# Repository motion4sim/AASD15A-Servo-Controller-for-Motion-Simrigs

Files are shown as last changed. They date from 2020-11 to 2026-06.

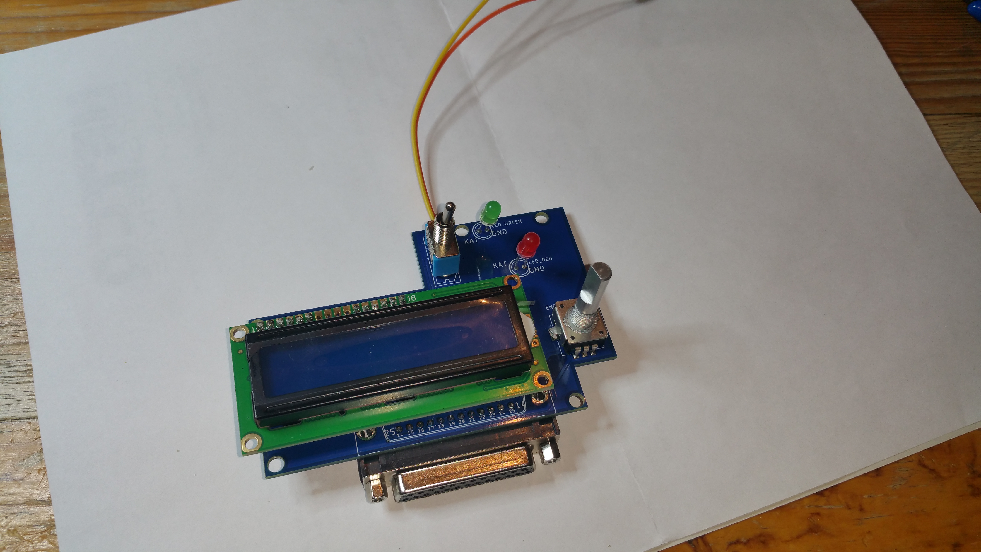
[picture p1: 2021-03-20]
diy_handheld/handheld-pcb-version/handheld-pcb-1 (3).jpg

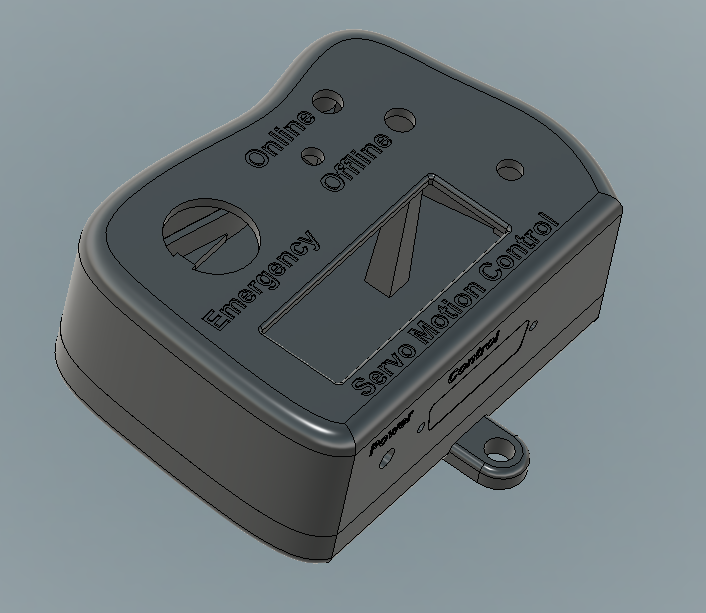
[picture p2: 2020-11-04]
diy_handheld/handheld_1.png

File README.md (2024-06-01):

# AASD15A-Servo-Controller-for-Motion-Simrigs

checkout our shop at motion4sim.com for more information

Motion4Sim M4S Controller Firmware

Version v3.30

- factory reset required after flashing!!!
- added Actuator Input Data matrix, 
- so you can use SRS or Simtools Actuator order without reconnecting cables
- edit via Handheld in Actuators menu or use Dashboard in Filter tab
- only for direct mode!
- in position mode you will need still clockwise actuator connection starting with 1 at front left actuator 
- fixed shutdown function torque recognition and not rebooting
- fixed service menu torque recognition

Version 3.29

- added separate fifo for usb motion and data
- in principle, both USB ports can be operated in parallel
  need to test what happens when Motion data is received on both ports
  so be carefull using it
- changed debouncing for killswitch and online switch
- improvement of serial pattern detection
- added SimHub  support

Version 3.28 

- added message crc datachecks to all communication 
- the end chars 0x0a 0x0d are replaced with crc16 checksumm
- still back compatible to 0x0a 0x0d if send to recieve but sends only with crc so older dashboard will not recieve data
- update to Dashboard Version 3.28
- works only full with Dashboard >=v3.28 because crc checks
- fixed motionusb port problems

Version 3.26

- just for testing fw updates with flypt

Version 3.25 fix1

- fixed  short brake release impulse when startup with EM Button engaged
- fixed  online speed set to 50khz only in some conditions

Version 3.25 official

- hardware pulsing is stable now ,just enable, works same, read advice in dashboard
- small change to break release delaytiming
- new spike algorithm is now implemented 
	-> adjust spikwindow for setup from smaller value to higher
	-> read also fw3.15 release note down this list
- old spike is emalp+spike2 option now in filter setting
- changed lowspeed in factory settings
- changed breakdelay to 100ms in factory settings
- @dureiken changed factory setting motionxp for spike to spike2 and cal/lowspeed settings
- no changes to dashboard made same version 

Version 3.24 

- a lot of changes test your rig behaviour before pratical use!!
- added new EM Button debouncing with Software and Hardware
- added prompt ">" for Setup and Configuration values
- fixed flashport at startup wrong config  data transmission 
- added transition to standby with special triple emalp filtering, 
	-> also into motion from standby uses now this transition
	-> setup transition speed for this its in seconds
- maybe for better transition adjust the low speed to 5000*10hz in setup (Speed from/to Standby Position)
	-> this also changes auto homeing speed for belt
- hardcoded service speed set to 1000x10hz before was low speed too
- extra01 pin is now low at startup in case for brake nc use
- controller firmware reset, now only possible in save rig states
- dashboard controls "transmit"  accepted only when restart/offline phase possible
- fixing service menu emergency issues
- changed doubleclick recognition speed a little bit faster 
- fixed belt spike2 problem (no spike calculation for belt)
- removed doubleclick feature in the menu

Version 3.20

-  removed motionsystem introduced in 3.10 -> done by Dashboard now
-  added support for flash-usb port for motion and dashboard use
-> i recommend this port now for all operations
-  added hw pulsing support for pcb version from 1.09 (could double resolution)
-  added option for inoffz. srs supp with native usbport mod
-  added support for new motioncueingsystem included in dashboard now
-  this fw operates only with dashboard version 3.20 
-  added realtime belt retreat modification 
-  added adjust.servobrake switching delay

Version 3.15 

- lcd init problems fixed everything else seems to emi related
- lcd only comes to garbled char when workhour timer is active (normaly deactivated)
- option in menu -> setup -> Mastergain enabl : if set to off Mastergain is fixed on main screen
- long press (>3s) of encoder button does a lcd screen init
- double click feature for encoder button
	-> fast double click switches main screen from 
		gain"100%" -> "Sp Win" Spike Window -> "Belt" retreat -> "Filter" Emalp value back to gain
	-> you can change value with encoder turning left or right
	-> values were not saved to eeprom
	-> for saving go to menu "Save and return"
	-> with double click you can also leave any menu back to main screen with no saving
- new Spike Filter design
	
	defined with 3 Values.
	
		Menu -> Filter 	-> Spike Filter 	
				-> Spike Window
				-> Sp.Filter smooth

	-> Spike Window:  from 1...400% (or more) 100%  is 1/4 actuator range in pulses
    	 	-this means if pulse input is more than say 100% (1/4 of actuator stroke) Spike is detected
		-pulsestrain is cut/limited to Spike window size pulsecount
	-> Spike Filter: 
 		- after Spike detection the Emalp(normal Filter) raises every frame(2ms) Spikestrength value is lowpass over raising emalp	
		-> this means lower value faster growing Filter (after spike slower return to normal motion)
		-> higher value ,lower growing filter ( after spike faster return to normal motion)
	-> Sp. Filter smooth:  when spike is finished (pulsetrain smaller as Spike Window)
		-> dyn Emalp filter decreases(2ms) with  Sp.Filter smooth ( Emalp over decr. value) 
		-> this means higher value slower decrease and slower return to normal motion
		-> and vice versa
	
	//for me follwing values have worked
	//Spikestrength = 20 to 80  (higher means more smooth in spike)
	//Spikewindow from 10%  for racing 20-40 % for flying  (higher means later spike detection)
	//Spike smooth 2-10   (higher means longer of spike smoothing ,do not use 1 never ending spike) 

Version 3.11 release

continueing lcd fixes
watch also 3.10 notice
- long press (5s) of encoder button does a lcd screen init

Version 3.10 release

Pay attention Motioncueingsystem is W.I.P. start with low scale first
Factory Reset is important for Motioncueingsystem to work
please install also latest Dashboard v3.10 for full use of Motioncueingsystem

-added full scripting motioncueing and filtersystem
-added autotuning system to scale the motioncueing profiles
-added system for storing motionprofiles in flash
-added doubleclick feautre for inputsystem
-added function to boot intobootloader in setup menu
-added support for new pcbversion 1.09 hardwaretimers

Version 2.23 release

- added dashboard support for belt configuration
- added working hour meter reset support ( press user button > 15 seconds for reset)
- lcd working now with no problems
- this fw support only until pcb v. 1.08
- last fw for this boards
- some code improvements

Version 2.19 release

- added belt actuator support
- added new emergency mode "keep online"
- added extra01 function send timer signal
- added sineloop for testing actuators
- added working hour meter
- factory reset needed from fw 2.11
- fixed most lcd problems but still not all yet :(
- better code perfomance
- cleanup 

Version 2.11

- added  support for SFX 3 actor  System in position mode
- no factory reset needed
- fixed homing issue with linear systems other then 6dof
- lcd garbage issue still exist _ screen reinit time now is shorter

Version 2.01

-complete rewrite of the motion engine
-now best motion ever 
-some smaler bugfixes (Service Menu)
-led blinking in some states
-code cleanup
-rewrite of serial port code
-rewrite of lcd display routines
-no srs support :)
Attention - for older first series boards there is also necessary to update the bootloader, contact me for this !!!

Version 1.60 Factory reset needed !! storage  changed

- included SFX RIG types in kinematics calculation BETA!
- activatet Native USB Port to work with Dashboard APP and Motiondata ->still not good as it should use MotionData port
- improved interface to Dashboard App
- load and Install also new Dashboard App

Version 1.54

- serial data interface  transfer extended for new Dashboard App
- works only with new DasBoard App correct,please update
- always do a factory reset after flash
- some bugfixes, linear factory reset, and 6dof float mode
- fixed srs

Version 1.51

Attention:	Factory reset needed !! storage  changed

- rewrite of service actuator moving functions
- usersettings moved to internal MCU flash storage  -> factory reset needed ! 
- factory reset possible with on board button (press 4 seconds for rotating Act setting and 8 seconds for linear Act settings)  
- stability of usb for apps improved
- update also to latest apps

Version 1.47

Attention: 	- eeprom data changed  _ after flashing do factory reset !

- fixed some servo7 bugs
- fixed linear actuator safety bug (safety >pitch)
- added function for servobrakes WIP
- added new transition to motion
- added adjustable time for transition to motion
- added offset for linear actuators
- added adjustable Online Position
- added adjustable Maximum Gain
- better actuator check function (also while homing)
- added shutdown function (drives actuators down to homing point and powers servos off; turn left in menu ) 
- smaller changes in menu texts
- some value checks added
- most new settings only from handheld adjustable actually

thanks to Dirty for testing

Version 1.42

Attention: 	- eeprom data changed  _ after flashing do factory reset !
		- save your settings to paper!! remote App changed data completely
		- install new Handheld app version
		- install new config app version

- added fully support for servo 7 ( remove some resistors on board before use)
- added support for infinite actuators
- bug fix of version 1.41_fix1 display stuck after flash
- some bugs fixed in srs autoconnect
- smaller changes in menu texts
- fixed bugs with remote handheld app
- changed actuator check function 

Version 1.41

-added interface for remote handheld app at native usb port
  (u have to wire the native usb port)
- minor code changes
- spikefilter led keeps on bug fixed
- transmit data from app doesnt reboot  fixed
- memory protection feauture inkluded
- updated bootloader for automatic software bootloadermode ( board delivered later as 062821)

Version 1.30

- added few remote commands for remote app testing features
- now fw has support for Sim Racing Studio in amcsd15a mode
- changed filter timing 
- minor bugfixes and code changes

Version 1.20

Attention: 	- eeprom data changed  _ after flashing do factory reset !
		- save your settings to paper remote App changed data completely

- complete new actuator settings, each actuator can be different , special for linear rigs seatmover
- keys and buttons using interrupts now
- native usb port on same70 board only for fw update
- remote app works now only with motion data port on breakout port
- remote app new version release for this firmware
- lcd fps setting now working
- new option for encoder direction

Version 1.19

- new data mode for floating point values from flypt mover
- changed some  motion cueing calculation for linear actuators
- improved 3d calculation to support center of rotation 
- fixed emergency button problems
- factory reset available for linear and rotating actuators
- remote app some minor changes
- fixed bug loading factory data when using remote app before calibrating

Version 1.18

- remote app expanded ,for now function only to native usb port
- native usb port and ftdi usb port working together now
- native usb port not for motiondata due to usb stack problems with pulse engine
- some changes to onboard motion cueing  now xyz koordsystem works like flypt
- motion cueing with linear 6dof rig works thanks to [GER]Basti-Discord

Version 1.17 Beta

- new usb remote configuration interface
- simple gui app  on github
- please check plattform after transmit configuration data controller will reset

Version  1.16 Beta

- change LCD - Display Init
- usb cdc code for target usb port (near ethernet connector) support asyn. cdc transfer
- enter bootloader via emergency-bt online-sw encoder-bt pressed and power on
- modified calculation of rotat. and linear inverse kinematics

W.I.P.

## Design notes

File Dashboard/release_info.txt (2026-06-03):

Motion4Sim DashBoard App

Disclaimer! this Software is free to use and in development. 
we explain that the controller from Motion4Sim is working indepently
and there is no need to use this software to operate.
we assume no liability for any damage caused by use.  
you use it at your own risk.

Release v5.36.2

- Hotfix for fw 5.37 Spike filter switching 
  -> related to fw changes
- added extension json config files for EC config data  

Release v5.36

- added new Onlinebutton Settings Latching NO/NC Momentary NC/NO
- correction of some Rig presets
- added WebDashboard URL configuration

Release v5.35

- added new Rigtypes support
- added shutdown backoff for actuator shutdown function
- update fw update with fw check and downloader
- added auto token function for offline license activation 

Release v5.34

- updated cfg exchange system to CBOR for increased flexibility
- switched cfg files to JSON (compatible with web dashboard cfg files)
note: older cfg files are still supported — load them and verify the configuration
- changed motor speed unit from frequency to RPM
- added EtherCAT configuration tab
- various minor improvements and fixes
- works with STm fw and latest Atmel fw

Release v4.30

- added support for Actuator8 WIND
- added presetmanager, when add new profile to motionsystem
- added wind support for motionsystem ( nolimits & xplane source support now wind) more to come
- added new Filter Syntaxes :
	ADD(VALUE; number)
	SETVALUE(VALUE; number)

Release v4.29

- new Inno Setup Installer ,small version github
  if it fails install manually before 
	-dotNetFx472_Full_x86_x64.exe
        -vc_redist.x64.exe 

- fixed cw/ccw showed wrong in actuator settings
- added lic update support for pro controllers

- new motion system with a lot of new features
- graphic Motion Telemetry Output
- 3d View for 6dof Rigs
- added new Belt Force System w.i.p.
- added Wind output to Com (experimental not directly tested)
- added OXRMC config GUI,when installed
- added basic mover import (limited function, only for filterstrings and 1. Pose is primary and second is ground)
- added Extra Effects Generator (Noise and Sinus only atm) 
  -> Noise can be casaded to have Asphalt layer maybe w.i.p.

- old profiles still supported import them

- added new gamesource Eurp.Trucksimulator2 &American Truck Sim.
- added Assetto Corsa Evo supp.
- fixed Nolimits2 gimbal lock problem
 
  Attention!!

  1. backup your profile from %appdata%/Roaming/Motion4Sim/motionprofile.xml
     normally it will not overwrite, but to be sure you have it save
  2. please be carefull its w.i.p. maybe there are some things will not work or cause problems
     i spent lot of time with it but i know i couldnt test everything !!
  3. do not forget to enable motionsystem in Config ->Setup Tab for using
  4. for networks setups please disable motion when using other motioncueing
      otherwise it will send also data to the rig !!!!

Release v4.25 fix1  

- re upload not zipped for Win11 virus false detection problem

Release v4.25

- added Setup Options for Switch/PushButton
- fixed some Profile saving/loading Issues
- added Support for Torgue Mode Actuator 7

Release v4.24

- added check for fw bin files, checks files for integrity (works from fw 4.24 no support for older fw files)
- added crc for bin
- checked source Condor2 is working also for Condor3
- added eth lan adapter checks

Release v4.22

- added latest values to edit from Dashboard
- added  udp support for new boards

Release v3.31

- added support for rFactor2 and F1-2024
- rFactor needs special plugin to work so 
- go to Config -> Source and  patch button will copy dll to rfactor plugin dir
- fixed config window minimize bug

Release v3.30

- config works only with fw 3.30 
- added Actuator Input Data matrix, 
- so you can use SRS or Simtools Actuator order without reconnecting
- edit via Handheld in Actuators menu or use Dashboard in Filter tab
- only for direct mode 
- in position mode you will need clockwise actuator connection starting with 1 at front left actuator 

Release v3.29

- added Source LFS
- added patching for LFS
- fixed flickering source combobox when connected, now combo is disabled
- fixed wrong gamedetecting  F1_23;DCS;Dirt when using same udp port
- fixed  ACC
- improved some gamedetection

Release v3.28++testing

- added  Source
	Nolimits2
	Automobilista2
	iRacing
	WRC
	BeamNG
- added Mover import for Filterstrings only
- added Patching for sources to work
- added support for different  motionprofile presets and smart editor for it		

Release v3.28

-added F1-2023 Game Source
-added Condor2 Soaring Source
-fixed  crc Problems with older FW
-for existing Installation add Profile from /program/motion4sim/profiles/motionprofile.xml
-or replace in %appdata%/motion4sim .. you can backup this file and reload your old profiles
-installer will not overwrite 
-added smart controller support

Release v3.28 testing - not much tested so far but works here  therefore it is tesing release

- added Dirt Rally 2.0 Dirt 4 support
- added crc checksums for data transmission
- added fw update checking and downloading
- added patch support for DCS and Dirt Rally 
- added openxr mc support in motionsystem
- added belt support for actuator 7 in motionsystem
- added profile  import and export features
- testing2: fixed comport vector overflow with mostly motionusb
- testing2: fixed msfs source not disconnect when closing msfs
- testing3: fixed xmlfileimport mapping
- testing3: changed german error lang
- testing4: added oxrmc changing gain with controller gain

Release v3.24

- added check for Transmit to prevent from restarting the controller 
  in unsafe situations

Release v3.20

- added Filter based Motion Cueing System 
- added Xplane, MSFS2020, DCS, Assetto Corsa Comp., Raceroom Source
- added High/Low Precise Timers for Filtersystem
- fixed Testpage bad Motion
- added support for Flash USB Port
- added some Option on Setup page
- only works with fw 3.20
- added some checks
- changed installer lang to english
- fixed em-state und extra01 state to combo boxes

Release v3.10

- added support for Motioncueingsystem
- fw 3.10 is recommend

Release v2.18 

- added belt config
- added disable autoconnect
- added using standart "comport" feature
- complete new code for communication
- testet with win 10 only
- changed and cleanup layout
- needs fw >2.23

Release v2.16 still Beta

- fixed homing speed data
- fixed crashing  App sometimes special with ftdi boards
- some layout changes
- added sfx 3 actor systems
- fw  >2.15

Release v2.15 Beta

- fixed flashing not working
- fixed autoconnect

Release v2.10 Beta

- code speedup
- changed Joysticksupport
- removed some buggy feautres
- underlaying api complete rewrite
- improved serial data connection

Release v1.60

thanks to Milligaus for developing C# Interface

- Handheld support to use controller with software only
- Configuration of all Settings in Config section of App
- Actuator 7 configuration will follow soon
- Memory Mapped File (MMF) support to run in Background while using Mover or Simtools
- UDP support is planned
- Software Keys and Buttons could assigned for OnlineSwitch and Emergency Switch functions
- Support for Gamepads,Joystick Keyboard Buttons (W.I.P.)

- sometimes problems with bluethoot devices please deactivate to be proove

for Memory Mapped File use

"Motion4Sim_tx"  to send data to Controller from Mover etc
or
"Motion4Sim_rx" to recieve answers from Controller

please report bugs to discord (Motion4Sim@4206)

thanks for using

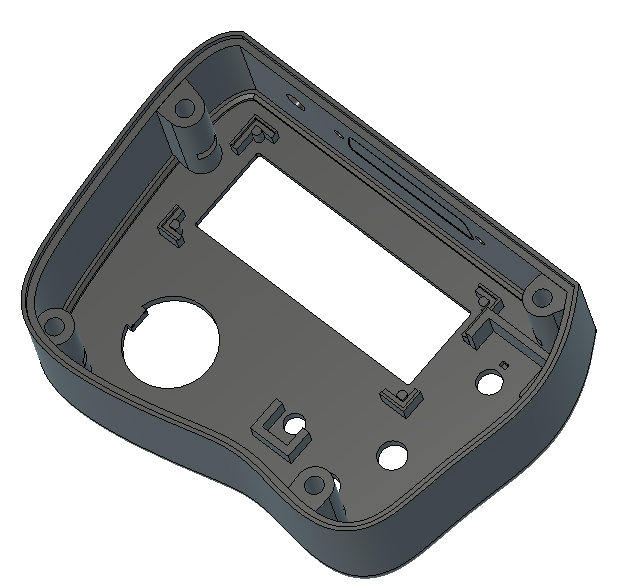
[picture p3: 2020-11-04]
diy_handheld/handheld3.png

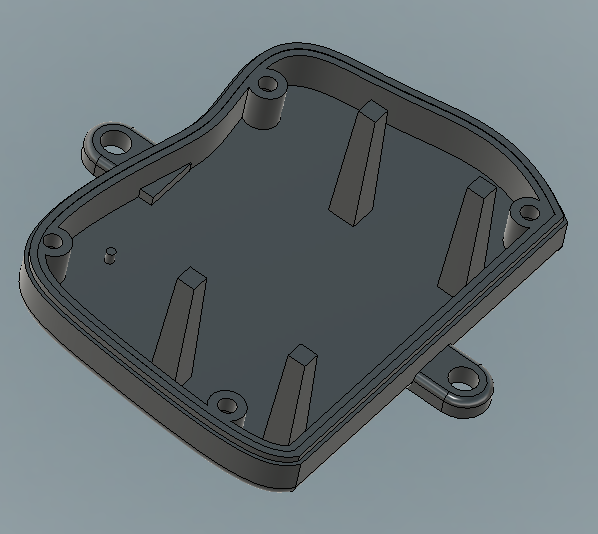
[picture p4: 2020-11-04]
diy_handheld/handheld2.png

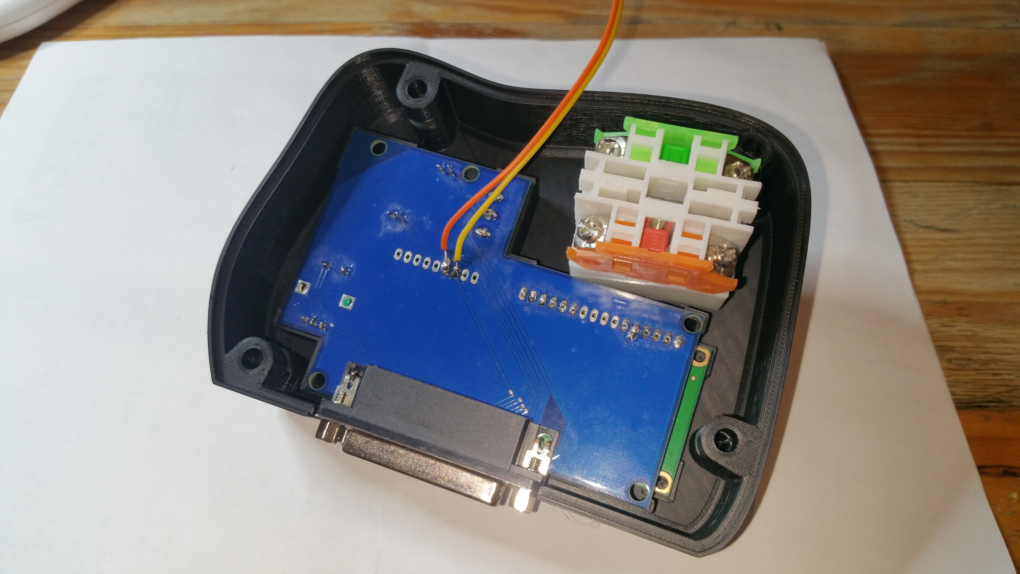
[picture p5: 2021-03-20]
diy_handheld/handheld-pcb-version/handheld-pcb-1 (4).jpg

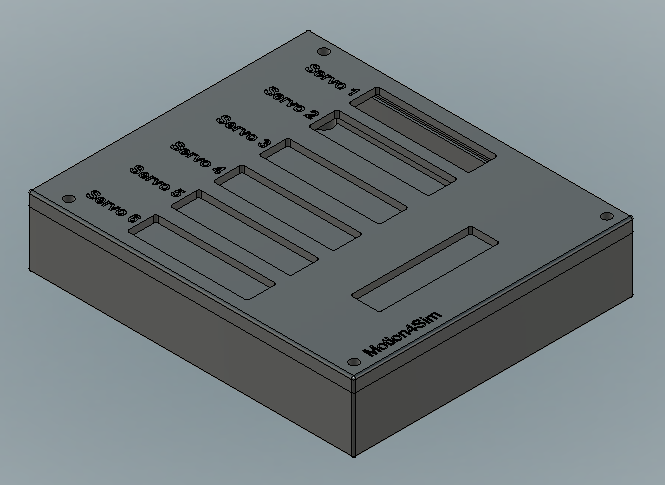
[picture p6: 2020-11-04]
diy_handheld/c_case_oben.png

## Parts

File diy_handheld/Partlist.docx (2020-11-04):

Partlist

1. Display 16x2

#### https://www.ebay.de/itm/LCD-1602-Blau-Display-HD44780-I2C-Anzeige-Bildschirm-16x2-Arduino-Raspberry-Pi/253723898777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

2. Encoder

###### https://www.ebay.de/itm/Rotary-Encoder-Drehregler-KY-040-Drehgeber-Taster-Poti-Arduino-Raspberry-Pi/392878965464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

3. Emergency Switch LAY37

###### https://www.ebay.de/itm/Not-Aus-Not-Aus-Schalter-Emergency-Stop-Pilzkopfschalter-Mushroom-head/162561518442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

4. Online Switch

###### https://www.ebay.de/itm/2x-MINI-KIPPSCHALTER-WIPPSCHALTER-KILLSWITCH-ECKIG-6MM-3A-KFZ-12V-VOLT/263098565064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

5. DB 25 Connector for solder female

https://www.ebay.de/itm/D-SUB-Buchse-25-polig-Lotkelch/184254619899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

1. 5V LED green and red

https://www.ebay.de/itm/3mm-LED-Sortiment-3-3V-5V-6V-9V-12V-red-blue-white-yellow-green-purple-12-Teile/283302538340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

1. holder for 5V Led

https://www.ebay.de/itm/10-Ledfassungen-f%C3%BCr-5mm-Leds-in-METALLOPTIK-Led-Fassung-Halterung-Montagefassung/370395657130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

4x Screw M4 x 30 mm and Nuts

some cable and solder tools

some pin male and female , shrink tubing

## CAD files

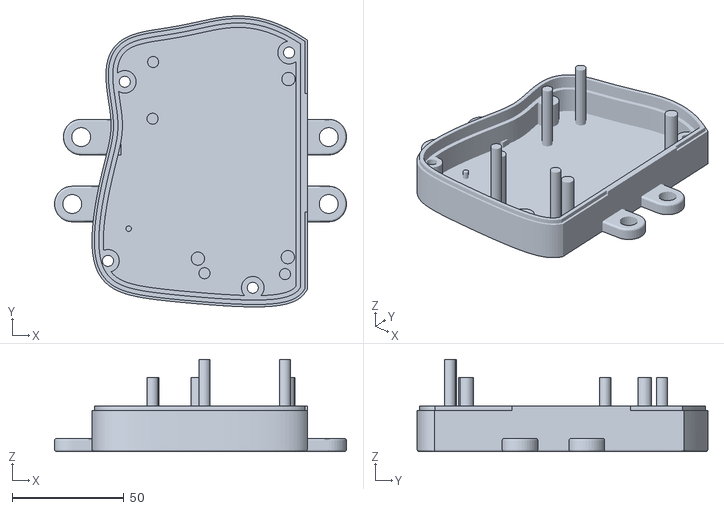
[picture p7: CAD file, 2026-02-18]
3d_print_files/handheld_back_pcb_30.stl
130.9 x 130.4 x 41.4

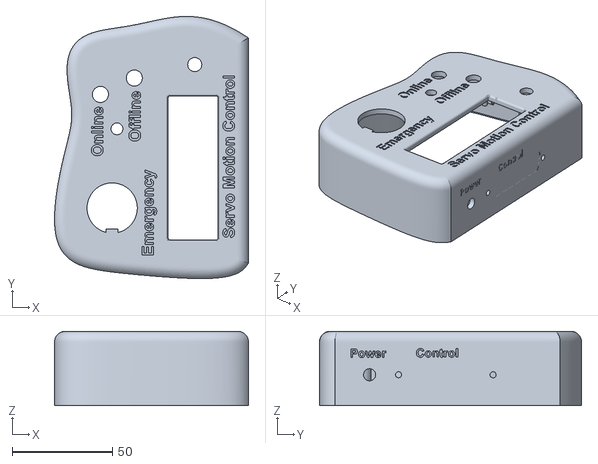
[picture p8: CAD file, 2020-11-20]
diy_handheld/Handheld_diy_top.stl
96.5 x 130.4 x 37.0

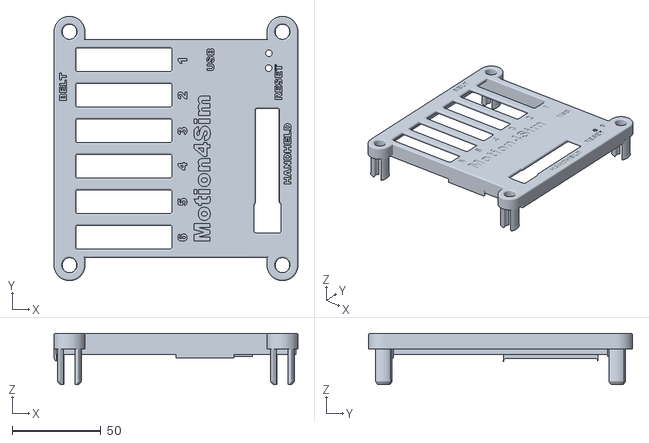
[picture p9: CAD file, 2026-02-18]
3d_print_files/pcb_top_m4s_v303.stl
137.5 x 148.9 x 29.0

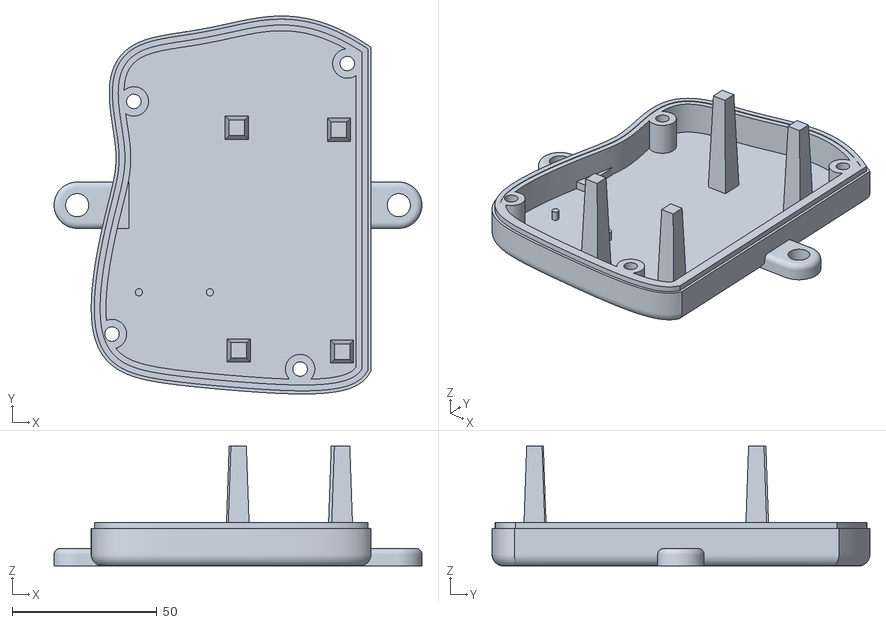
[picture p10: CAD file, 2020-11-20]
diy_handheld/Handheld_diy_back.stl
127.0 x 130.5 x 41.4

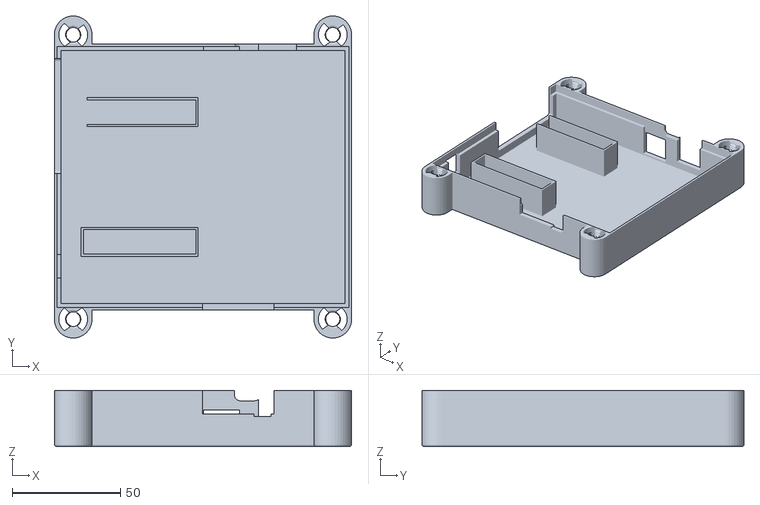
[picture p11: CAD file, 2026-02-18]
3d_print_files/pcb_btm_m4s_v303.stl
137.5 x 148.9 x 26.0

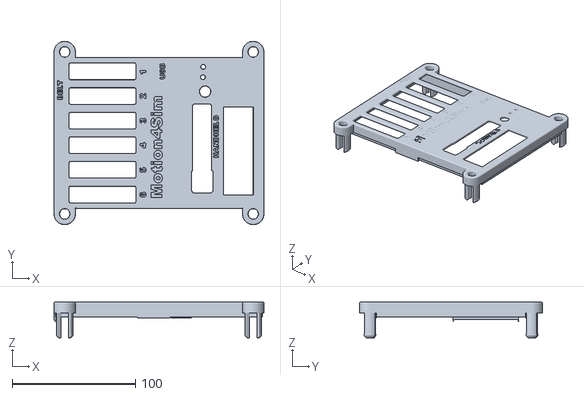
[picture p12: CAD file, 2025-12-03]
3d_print_files/pcb_case_display_top_motion4sim_v203.stl
170.5 x 148.9 x 29.0

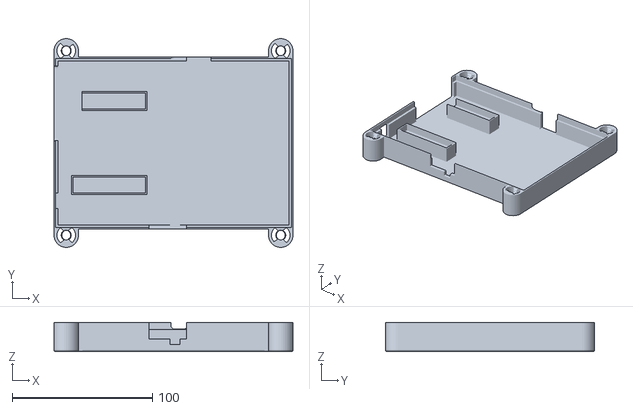
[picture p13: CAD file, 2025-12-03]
3d_print_files/pcb_case_display_bottom_motion4sim_v203.stl
170.5 x 148.9 x 21.0

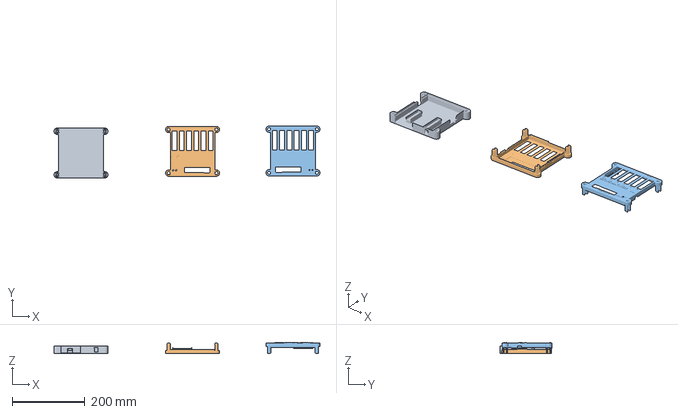
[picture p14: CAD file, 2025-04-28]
3d_print_files/2ColorPCBCase.3mf
732.6 x 143.0 x 31.4 mm
pcb-case_m4s_v203_bottom.stl
exported flat.stl x 2

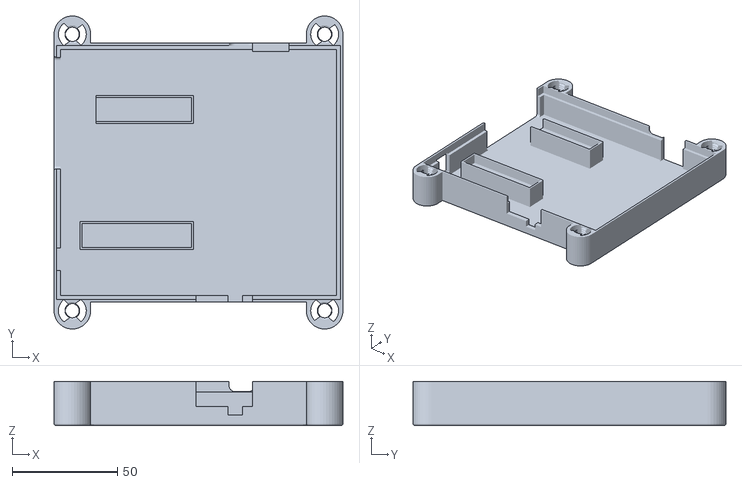
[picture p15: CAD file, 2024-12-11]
3d_print_files/pcb-case_m4s_v203_bottom.stl
137.5 x 148.9 x 21.0

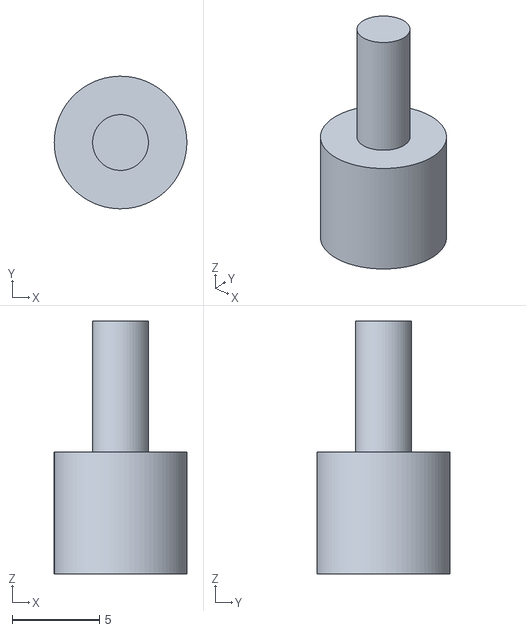
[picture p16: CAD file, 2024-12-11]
3d_print_files/pcb_case_button_v203.stl
7.60 x 7.60 x 14.5

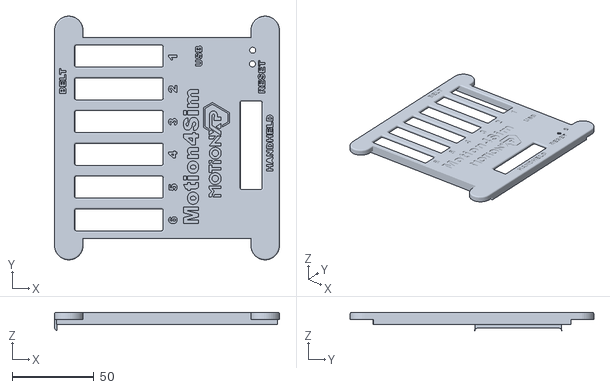
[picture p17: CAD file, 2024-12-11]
3d_print_files/pcb_case_top_motionxp_v203.stl
137.5 x 148.9 x 11.2

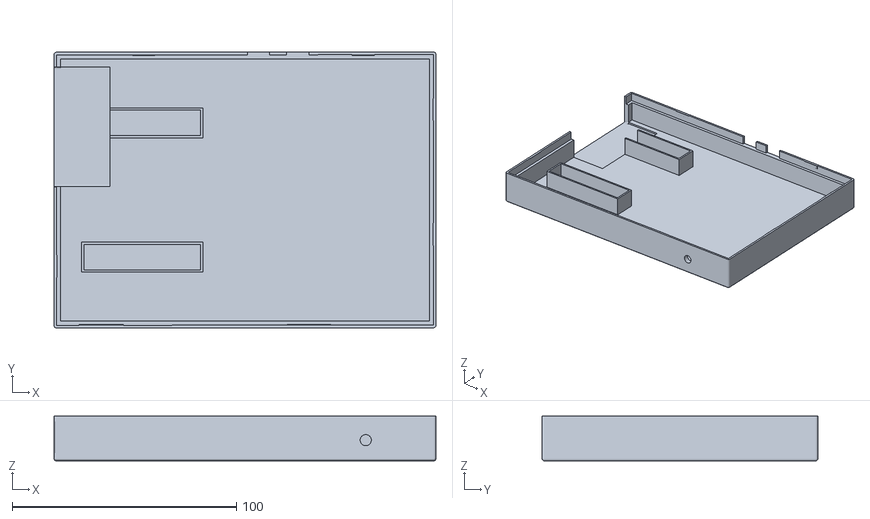
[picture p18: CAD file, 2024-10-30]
3d_print_files/gehäuse_bottom_pcb_v115mitdisplay.stl
170.5 x 123.0 x 20.0

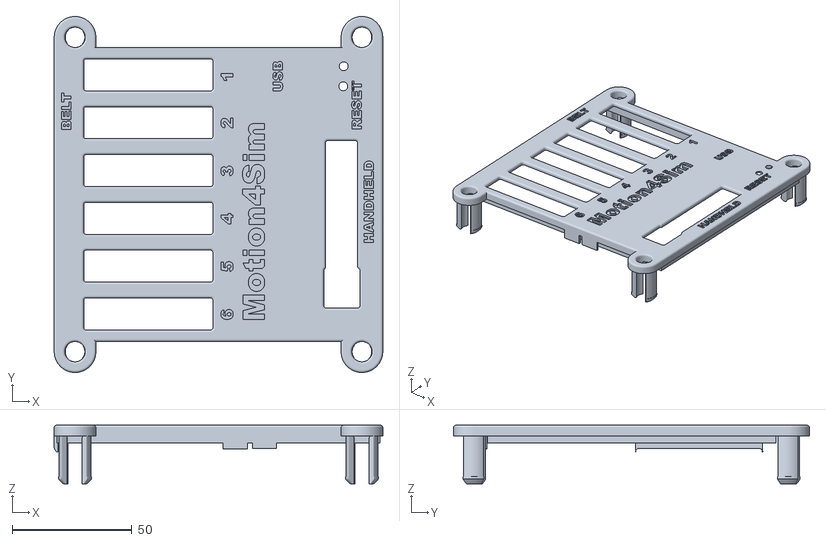
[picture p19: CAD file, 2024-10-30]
3d_print_files/Case_Top_m4s_1.15.stl
137.5 x 148.9 x 24.5

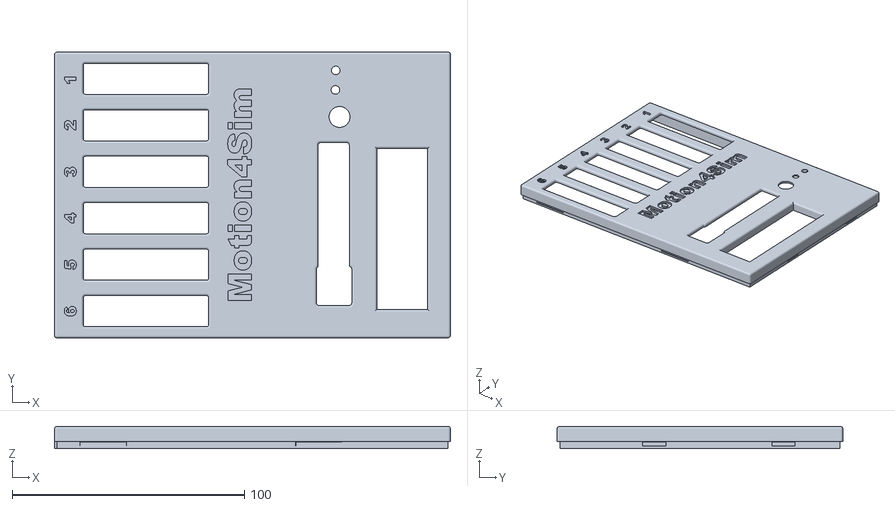
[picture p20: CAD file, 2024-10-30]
3d_print_files/gehäuse_top_pcb_v115mitdisplay.stl
170.5 x 123.0 x 9.50

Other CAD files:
3d_print_files/pcb_case_top_motion4sim_v203.stl
3d_print_files/gehäuse_top_pcb_v110_display.stl
3d_print_files/pcbcase_v1.10_button.stl
3d_print_files/gehäuse_down_pcb_v110_display.stl
3d_print_files/handheld_top_pcb.stl
3d_print_files/old_board/Controller_case_oben_lcd_enc_v1_04.stl
3d_print_files/old_board/Controller_case_oben_v1_04.stl
3d_print_files/old_board/Controller_case_unten_lcd_enc_v1_04.stl
3d_print_files/old_board/Controller_case_unten_v1_04.stl
3d_print_files/old_board/gehäuse_down_pcb_v110_display.stl
3d_print_files/old_board/gehäuse_top_pcb_v110_display.stl
3d_print_files/old_board/pcb_case_1.07_mysimkit_bottom.stl
3d_print_files/old_board/pcb_case_motion4sim_down_v1.10.stl
3d_print_files/old_board/pcb_case_motionxp_top_v1.09.stl
3d_print_files/old_board/pcb_case_motionxp_top_v1.10.stl
3d_print_files/old_board/pcb_case_mysimkit_down_v1.09.stl
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

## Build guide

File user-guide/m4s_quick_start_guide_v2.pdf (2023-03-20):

# Motion4Sim

2023

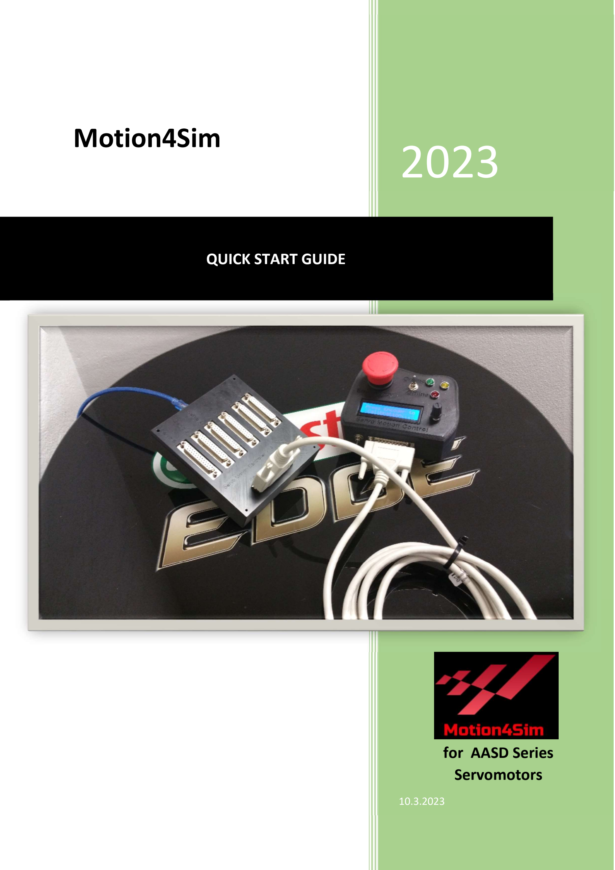
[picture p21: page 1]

for AASD Series
Servomotors

10.3.2023

QUICK START GUIDE

f o r b e t t e r

pe r f o r m a n c e

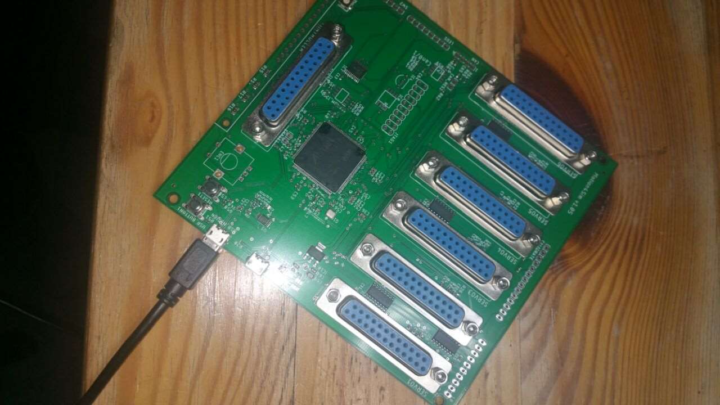
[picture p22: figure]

1

In these instructions we briefly describe how you can quickly put the controller into operation. For the first test, please use the motors without a connected load. Please be aware of the risk of injury if you use the motors improperly. For Information not described here, please read the manual.

### 1. make sure that the servo motors are not supplied with power

### 2. connect all cables needed to the motion4sim board

a. USB Cable to USB Motion Port on pcb board
b. D Sub 25 Cable 1-6 to the Servomotors (or opt. 7)
c. D Sub 25 Cable for handheld device if no display and encoder is installed
d. If display and encoder are installed , connect a online switch to connector SW2 and a emergency switch too (more details in the manual)
e. Or use the Dashboard app instead of c. or d.

### 3. Plugin the usb cable into computer or other 5v usb source

f o r b e t t e r

pe r f o r m a n c e

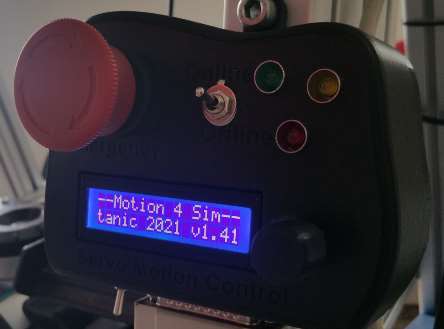
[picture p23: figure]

2

### 4. Controller boots up

### 5. Do factory reset by turning the encoder to the left and choose kind of

rotating- or linear actuator factory reset. enable with pressing encoder button. If the encoder works wrong direction check next point.

6. after the factory reset is done the controller resets and boots up again.

### 7. wait until is rebootet and press the encoder button

### 8. Check encoder turning direction , you can see the master gain rising or

reducing. Also check the behave oft the emergency button.

mastergain in the down left corner in %

right turn should rise and left turn should reduce master gain. It is possible that some encoders have other direction. This could be changed in the setup menu. (compare to manual)

f o r b e t t e r

pe r f o r m a n c e

3

### 9. Press encoder button and search by turning left/right the setup menu

entry. Press encoder button and turn encoder left/right until found „encoder direction“. If the emergency button is also not correct please change in the setup menu the option „Emergency NC“. Some emergency buttons are only „normaly open“ or „normaly closed“ other have both , in the setup menu you can change the behaviour oft he emergency button. If all settings are made, use the menuentry „back“ to get to the upper menu-level.

10. Now set the number of installed actuators in the menu. ->Actuators->Number Actuators(last entry)

The assignment of the connections is only important if you want to use the check actuator function. Otherwise the connections can be connected as you like. If you want use the check actuators function. Make sure to connect the actuators in such a way that the connections of the actuators in ascending order from 1 are fully occupied without any gaps. For example 1,2,3,4 or 1,2 or 1,2,3,4,5 and so on.

Now set all the actuator specific values.

Rig -> to Rotary or Linear Custom etc
Encoder PPR,
Electron.Gear ,

for rotating actuators:
Gearbox Ratio 1:,
Rot.Range,

for linear actuators:
Leadsrew Pitch,
Actuator Length
Lin. Act. Safety

Check also in
menu->Actuator->Actuators->Actuator1..8 submenu->Rotation:

f o r b e t t e r

pe r f o r m a n c e

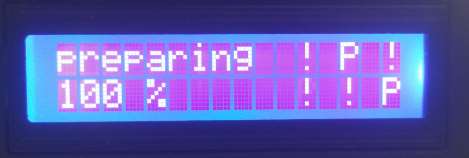
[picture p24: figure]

4

for cw or ccw rotation direction for each connected actuator.

most values are preset usefull

11.If all settings are done turn encoder to the rigth until you have a menu entry called „back“ , activate by pressing the encoder button. Repeat this until you have the upper menu and the last entry by turning to the rigth is „save and return“. Press encoder button to save the settings to eeprom. You have to use this function everytime you change values.

### 12. Only in the first run you should repower the controller , when all

settings have saved then execute the reset option in menu.

13.Now power the actuators.

14.After controller reboots press encoder to home.

15.The actuators should now searching for home position. They are searching for a hard stop or running for home switch to trigger. Check that all actuators are turning to the correct direction. If something goes wrong hit the emergency button for stop. Change the settings and repeat. Homing is essential for the controller to work properly.

The display shows :

X: for unconnected motors
P: for homing motors (preparing)
!: for running to park or safety position R: for Ready

f o r b e t t e r

pe r f o r m a n c e

5

16.If they are ready , the display shows „R“ for each actuator. You can switch off the online switch. If the switch is already at off position you can switch online and the actuator moves to standby position and is ready for recieving data.

### 17. Check the range oft the actuator carefully so that the selected values

causes no hard crash of your hardware

18.read the manual carefully, if you have problems contact support.

### 19. For easier configuration there is an Dashboard app. You can download

from here

https://github.com/motion4sim/AASD15A-Servo-Controller-for-Motion-Simrigs/tree/master/Dashboard
Please note the dashboard app has problems in win11 .
Close all Serial scanning apps like srs. If the app won´t connect to Controller please try following.
Remove all unneeded USB-Serial Devices and deactivate Bluetooth –Serial Devices.
If changes were made in the Configuration you always have to „Transmit“ the data to Controller.

### 20. thank you for using motion4sim and enjoy

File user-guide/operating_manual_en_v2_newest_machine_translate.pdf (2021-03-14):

# operation manual

2020

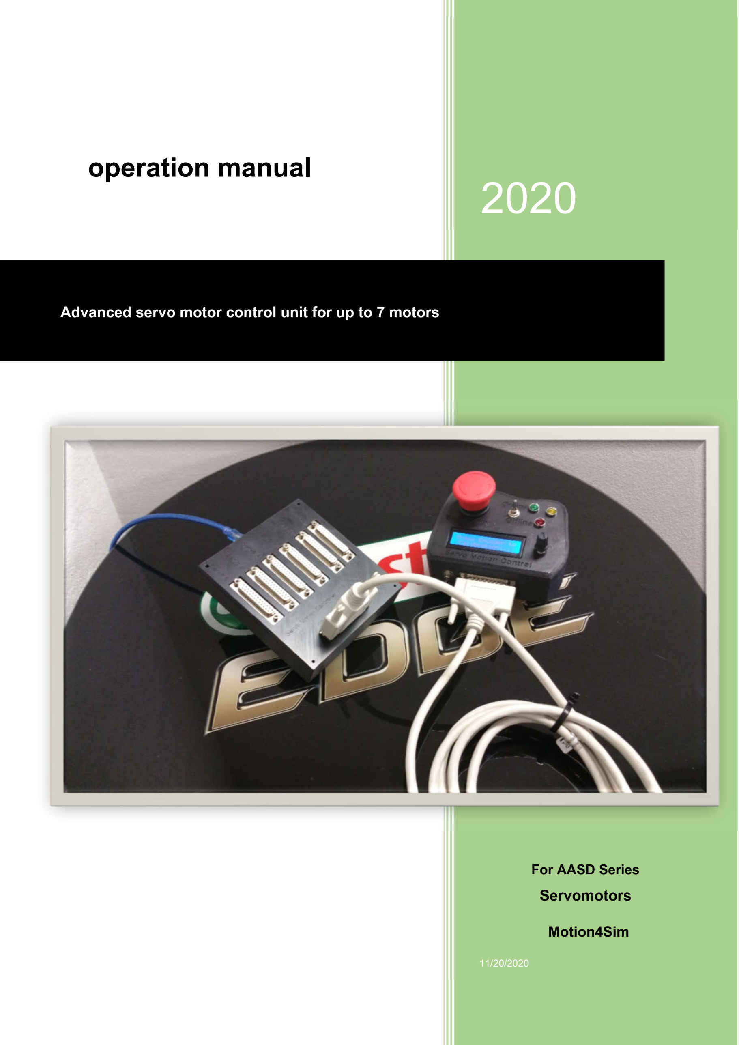
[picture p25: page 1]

## Advanced servo motor control unit for up to 7 motors

### For AASD Series

## Servomotors

### Motion4Sim

11/20/2020

## contents

Hardware cabling | 8th
Servo motor amplifier wiring | 8th
SET UP | 19th

1

introduction

The M4S-AASD15A servo controller enables the fast and seamless transfer of movement information from the PC simulation to the servo motor. The data exchange takes place between the interface programs such as Simtools, FLyPT Mover, BFF, etc. and the simulation.

The interface software calculates the motion vectors and forwards the values to the M4S servo controller via the USB interface. This controls the servomotors and also offers the option of calculating and smoothing motion cues yourself. The servo motor output stages are connected with DB25 cables.

All parameters necessary to operate the many actuators and actuator types are freely adjustable and configurable. All common servomotors that support STEP / DIR can be used.

2

## Functions

The controller was mainly designed for the AASD servos. However, other servomotors can also be operated with it. It can be used to operate all servomotors whose amplifiers are operated via the Step / Dir function.

The following functions are operated by the controller:

Hardware functions

1.
2.
3.

4th
5.

6th
7th
8th.
9.
10. 32 bit processor

### 11. Save the settings 12. Control of LEDs for status display (external handheld) 13. Housing (to print yourself)

14.Control unit can be installed 3m away (optional)

### 15. LC display and encoder can also be installed on the mainboard

### 16. Automatic home calibration on power up or re-connection without limit switches

### 17. Limit switches can be optionally installed for home calibration

### 18. Protection from exceeding physical limits of the actuator 19. Optional Platform Health check, to ensure all actuators are active during gaming 20. Latency as low as 1ms in Mover and Simtools or faster if some tool will support 21. E-stop, Force Offline buttons and switches

### 22. Usb power supply

Control of 6 + 1 servomotors (optional) Pulse speed up
to 550 kHz
Step / Dir fashion
Query and evaluation of torque (for calibration) as well as error status, display of parameters via LC display 16x2, full menu
Operation via rotary encoder with pushbutton switch for
signal reception
Emergency stop switch for the servo functions. Serial USB connection for data transfer

Software functions

1.
2.
3.

4th
5.

6th
7th
8th.
9.

### 10. Adjustable stroke unlimited

Software is menu-driven and easy to use
All functions can be parameterized to meet your own requirements. Monitoring of the status of the motors
Automatic calibration of the zero position Servomotors calibration also possible via limit switches
Service function for repair or control position of the motors Manual control of each motor individually for testing and maintenance Adjustable direction for Inline or Foldback placement of servomotor Adjustable screw lead pitch advance per revolution freely adjustable

3

### 11. Selection of belt reduction ratios or gear ratios freely adjustable

### 12. Rotating and linear actuators are supported

### 13. Scaling of the input signals (master gain)

### 14. Real exponential moving average filter for anti-vibration and smooth pulses on the

actuator
15. advanced full adjustable spike filter to automatically eliminate jolts during crashes or unwanted motion cues

### 16. Offset for each motor (especially for rotating actuators)

### 17. Variable parking position

18. Actuators individually adjustable (electronic translation, length of the act., DOF system)

### 19. Speeds for calibration, slow speed and high speed freely adjustable (max. 550 kHz)

20.Inverse kinematics with> 1000 calculations per second (for linear and non-linear actuators)

### 21. Geometry for steward platforms with 6 DOF and 6 actuators individually adjustable

### 22. Wash-out filter for each axis (can only be set with inverse kinematics)

### 23. Evaluation of 24 bit input data (Simtools / Mover)

### 24. Calculation in 32/64 bit for maximum smoothness of movement

25. 2 different operating modes: direct or inverse kinematics

4th

### PCB and connectors

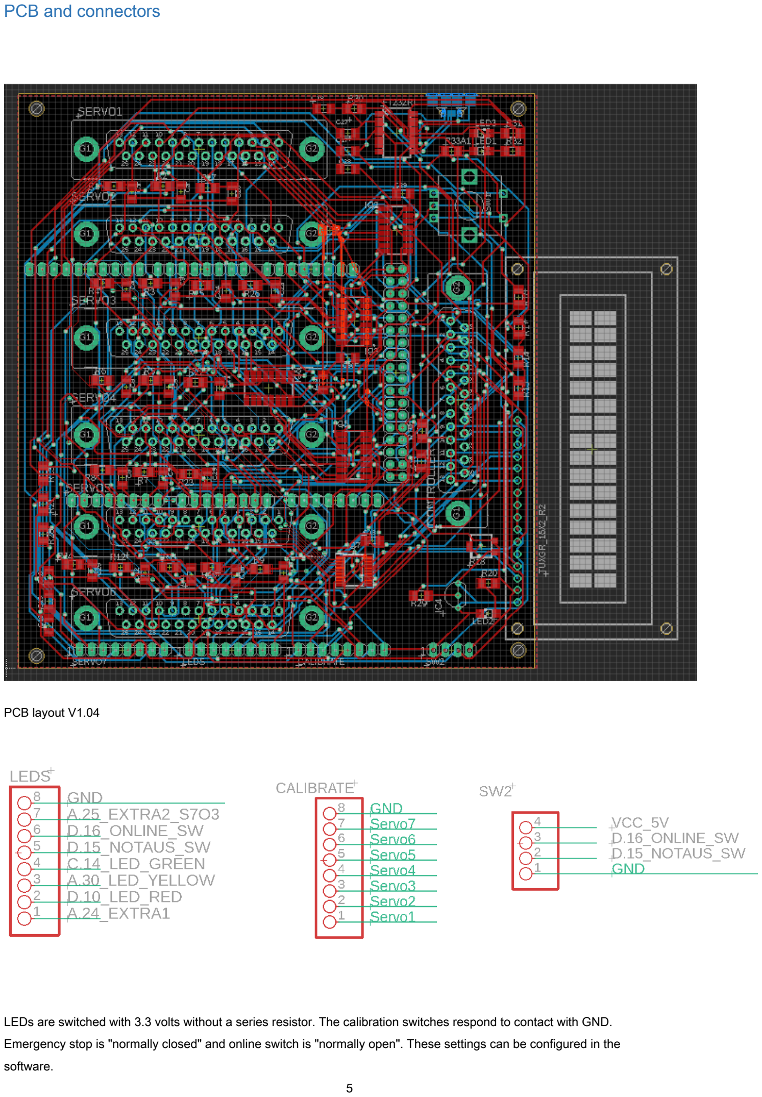
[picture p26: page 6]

PCB layout V1.04

LEDs are switched with 3.3 volts without a series resistor. The calibration switches respond to contact with GND. Emergency stop is "normally closed" and online switch is "normally open". These settings can be configured in the software.
5

Danger:

The micro USB port is sensitive to mechanical stress, please work with caution when trying it out.

Handheld Connector

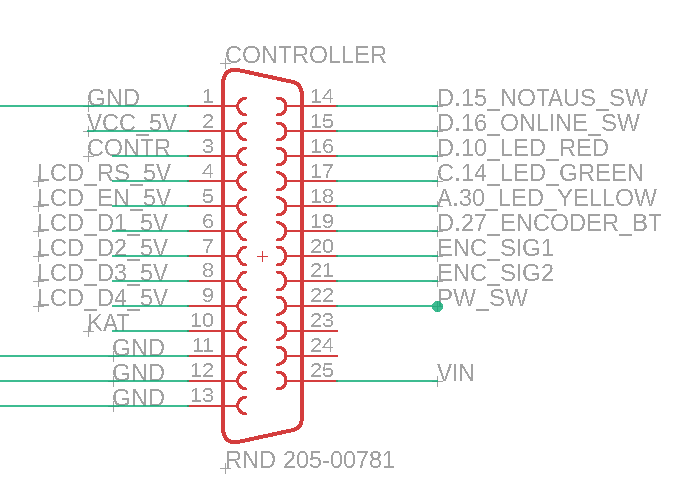
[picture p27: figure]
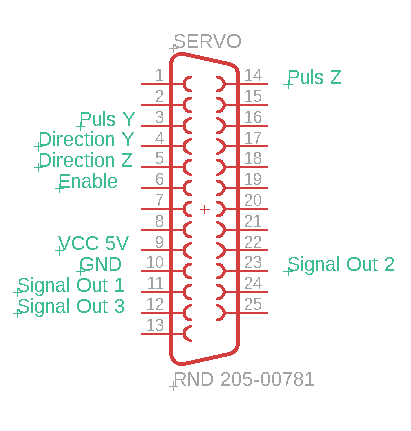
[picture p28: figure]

6th

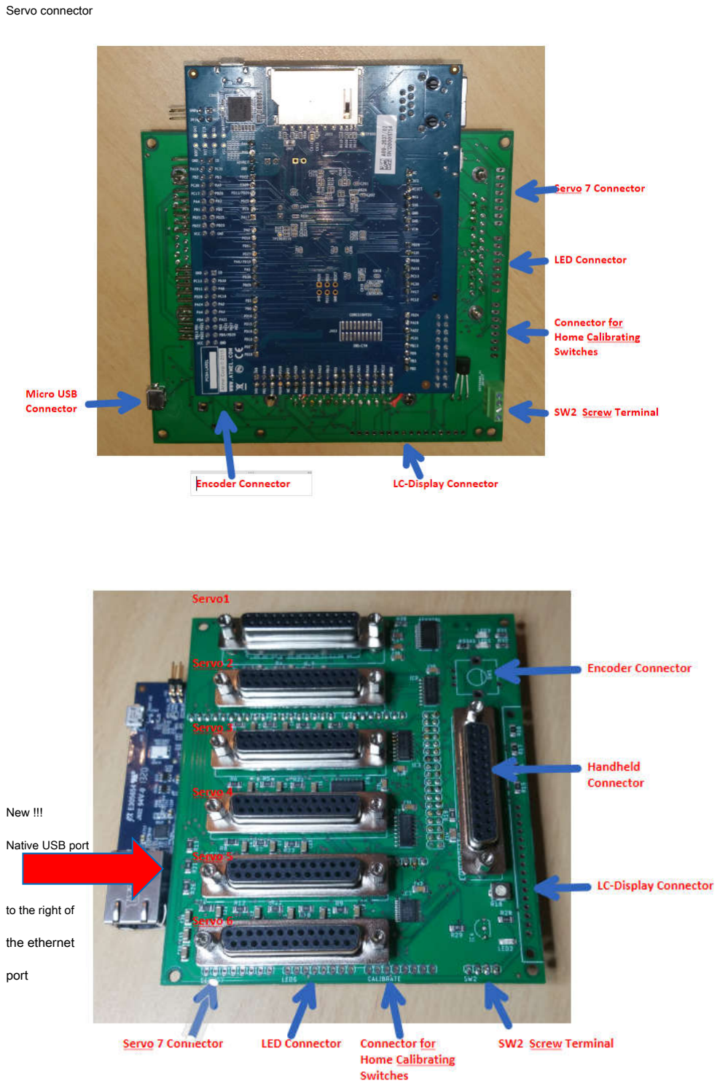
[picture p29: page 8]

Servo connector

New !!!

Native USB port

to the right of

the ethernet

port

## Hardware cabling

Servo motor amplifier wiring

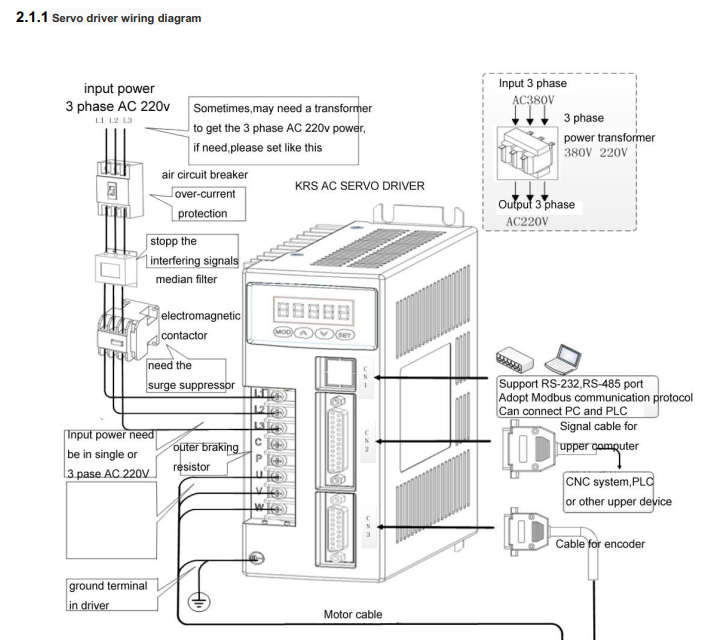
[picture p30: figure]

The mains voltage connections are partly different, please always consult the manufacturer's data sheet. For example, see also:

https://github.com/motion4sim/AASD15A-Servo-Controller-for-Motion-Simrigs / tree / master / Manuals

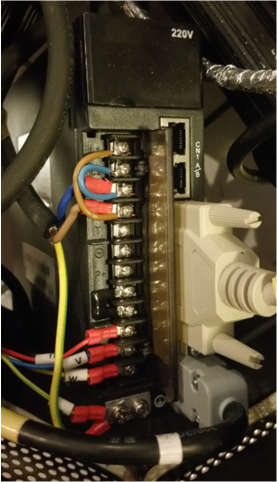
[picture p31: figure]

8th

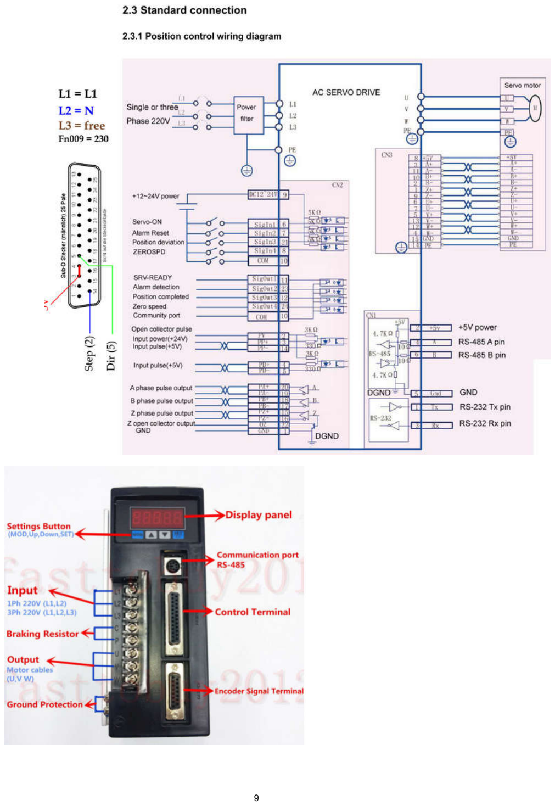
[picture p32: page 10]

9

## Settings of the servo amplifier

The controller can be connected to all servos that have a DB25 connection. It is also possible to manufacture your own adapter cables. Ask about compatibility.

AASD-15A Servo Settings:

Push MOD until you see Pn000. This enters the parameter mode.
Change and check these settings on all motors:

FN9 = 230 (230Volts recommend) Check this value if you get errors

Pn8 = 300
Pn9 = -300
Pn51 = 3000
Pn98 = 1-20 - Pulse Multiplier (electronics gear) different to Thanos and SFX for higher resolution

Typically on M4S you can set this to PN98 = 2

PN98 = 1 has to test with EMV interference of your construction by pulsing higher than 300 kpps

Pn109 = 1 - smoothing, 1 = fixed smoothing, 2 = s-Shaped smoothing Pn110 = 30 -
Smoothing Filter Time
Pn113 = 20 - Feedforward%
Pn114 = 10 - Feedforward Filter Time (ms) Pn115 =
100 - Gain%
Pn24 = 100

Pn51 = 3000 motorspeed (2500 or 3000 mainly) Pn52 = 1 signal port 1 servo enable
Pn60 = 2 Sigout Port 1 Servo ready Pn61 = 6
Sigout Port 2 Servo Treach

Pn62 = 4 Sigout Port 3 Servo Preach

10

Hand-held device

For more information see also

https://github.com/motion4sim/AASD15A-Servo-Controller-for-Motion- Simrigs / tree / master / handheld

and

https://www.thingiverse.com/thing:4641555

11

## Setting the controller / menu control

When you switch on the controller or supply it with USB voltage, the display is activated and loads the last settings used from the memory. It then waits for user input. When you press the encoder, the automatic calibration is started. There is also the option to turn the encoder to the left. This enables you to access the service menu without performing the calibration. (2nd picture) if you turn the encoder further to the left, there is still the option of performing a firmware reset. (Fig. 3) Caution, all settings will be lost.

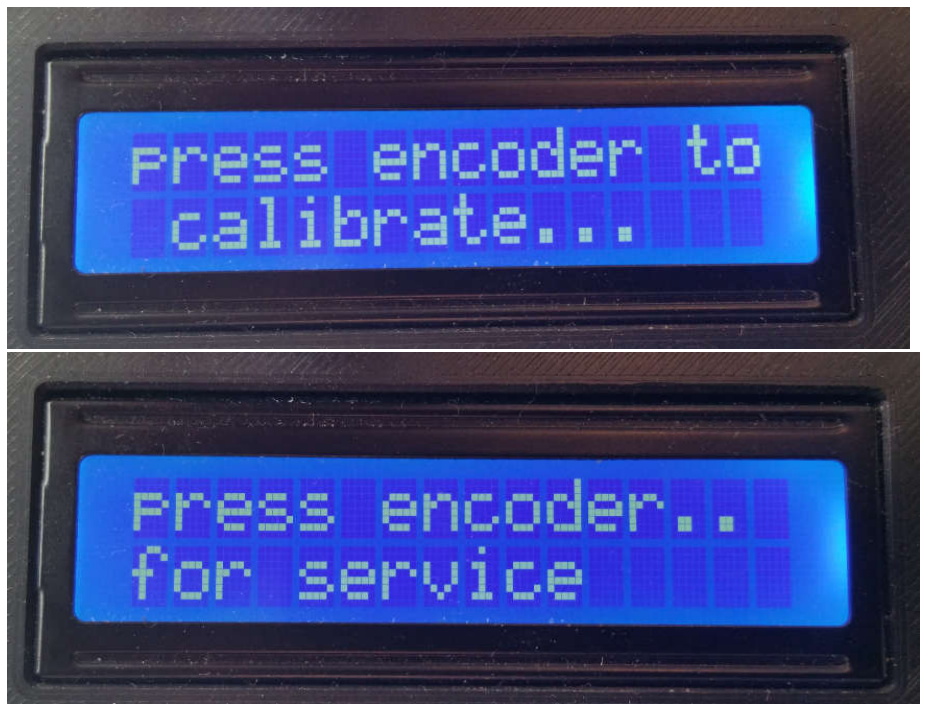
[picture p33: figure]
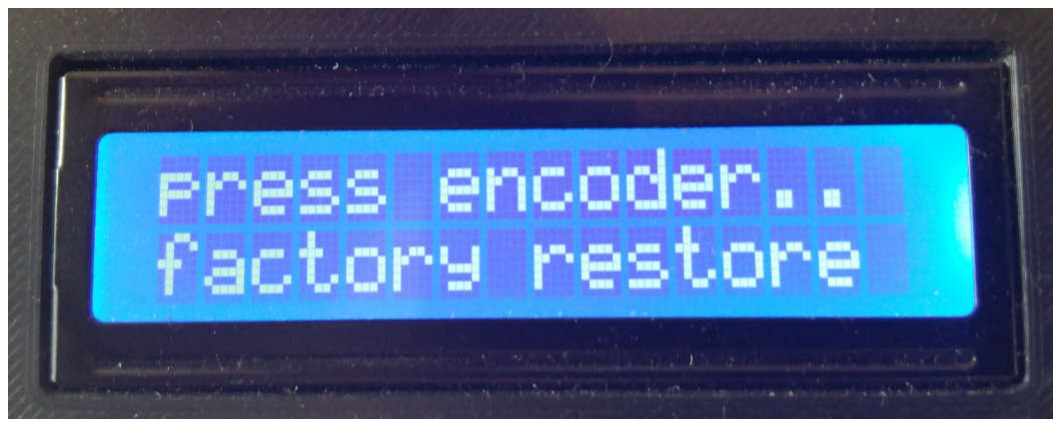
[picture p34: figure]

12th

In the first case you get to the main screen after pressing the encoder button. Here the status of the first 6 actuators is shown on the right.

X | is | Offline
C. | is | Calibrate
P | is | Preparing (moves to the parking position after calibration)
! | is | Employed
R. | is | Ready to use for motion data

The status of the rig system and the movements the machine is making are shown in the top line of the display.

to parkpos ..
preparing ..
emergency ..
offline..
ready ..
standby ..
wait uart ..
on-line..

moves to the parking position
calibrate and move to offset position Emergency stop switch activated
Offline switch activated according to online status System fully calibrated
Moving to the home position
in home position waiting for serial data
Serial data is received and movement takes place

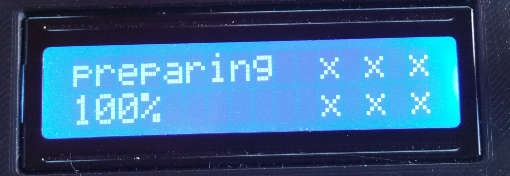
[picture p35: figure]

Functions of the encoder on the main screen:

The status of the master gain controller is displayed at the bottom left. (100%)
If you turn the encoder to the left or right, you reduce or increase the amplification of the pulses in 10% steps. The gain has a range of 10% - 400%. The gain can also be changed in online mode.

If you press the encoder you activate the submenu structure. The menu structure is divided as follows.

### 1. Calibrate

### 2. Filters

### 3. Service 4. Actuators 5. Setup 6. Rig 7. Kinematic

- automatic recalibration
- Output filters
- Menu for manual actuator movements
- Actuator settings
- Settings of the controller
- Settings for Stewart geometry
- Input filter for DOF data

13th

### 8. Reset

### 9. Save and return

You can navigate through the menu structure by turning the encoder to the left or right. Activate the respective menu item by pressing the encoder.

- Restart the controller
- Save the current settings and close the menu

## Filter menu

The following options can be set.

Filter enabled:

Switch the filter on or off

Filter type :

SMA (not used anymore)

SMA & SPIKE (not used anymore)

EMALP Exponential Moving Average Low Pass Filter (as in Mover) EMALP & SPIKE

Filter samples:

Strength of the selected filter. The larger the value, the smoother the movement

Spike filter :

This filter is designed for excessively strong unwanted movements. Spike Window which, if exceeded, activates the filter.

100 corresponds approximately to the pulse spacing of half of all possible pulses of the actuator. Try it out for an optimal setup. The lower the value, the sooner the filter is activated. With 1, all pulses are filtered.

_bithalf * RIG . Spikewindow * RIG . Spikewindow *
RIG . Spikewindow | / 10000000;

Spike Strength:

This value influences the smoothing of the pulses if the spike filter was activated by exceeding the limit. The strength increases exponentially (filter ^ 4̂) the greater the overshoot of the window.

14th

Sp.Filter smooth:

The spike filter operates dynamically and changes the smoothing accordingly. Therefore another EMA filter was built in for the dynamic change, which is controlled by this value.

Small value Spike filter increases quickly and jerkily when triggered and also returns quickly and jerkily after the end of the spike.

Value large Spike filter increases more gently when triggered and also returns more gently to the initial filter value.

(deactivated)

Logistics filter compresses the pulses for the actuator using the factor

Logistic Factor:

Larger value Steeper rise (blue) Smaller value

weaker rise (green)

With a smaller increase, the maximum also becomes logistically smaller

Back : | Closes the submenu and returns to a level above

15th

## Service menu

This menu is for testing the actuators and for moving the actuators to special service positions. All actuators can be moved simultaneously or each one individually. After activating the respective submenu, the value of the actuator can be increased or decreased by turning the encoder to the right or left. The value is changed by the value saved in "Multiplier". This menu can also be reached directly when starting the controller without calibrating the actuators. This can be used, for example, to “jack up a Stewart platform” in the event of a repair. A calibration is carried out when the menu is exited.

This function can also be used to save the offset of the individual actuators and all actuators. For Change Offset, set "Yes" with the encoder and confirm with Push.

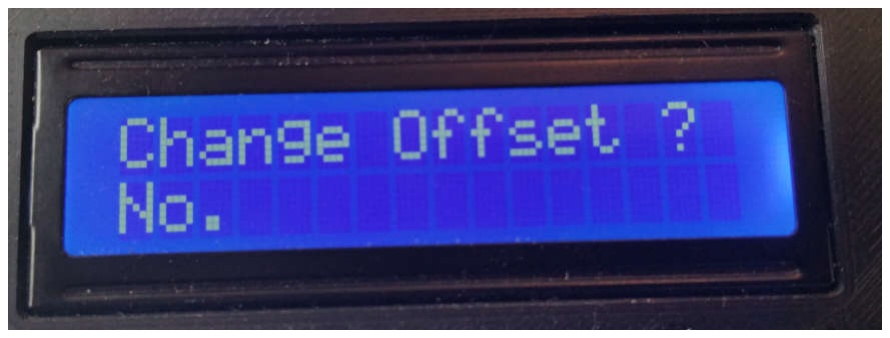
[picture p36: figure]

Repair - moving without calibration

Attention be careful:
Start the controller, note that the emergency stop button is not pressed is. Choose

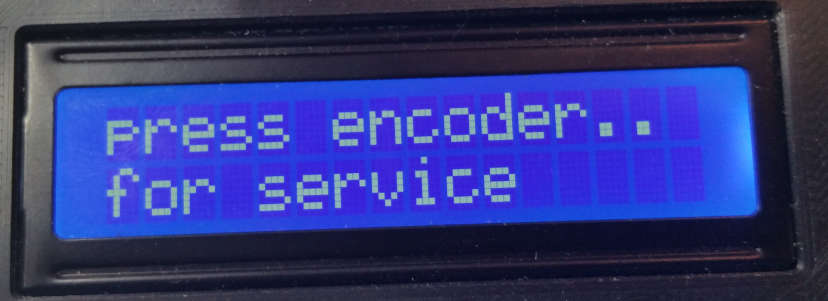
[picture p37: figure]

Move the encoder right or left and select one or all of the actuators to move.

Attention, after exiting the menu, a calibration is carried out.

If you press the emergency stop button, the servos are deactivated depending on the setting in the setup.

16

## Actuators

Actuator | :

Linear or rotary

These values are used for the calculations of the inverse kinematics as well as for calculating the resolution of the actuator.

Encoder PPR | : | Number of encoder positions depending on the servo with AASD15 10000
Electronics gear | :

Required for the calculation of the actuator resolution

PN (98) value from the servo output stage must be the same for all actuators

Ratio of used gears. Only reduction possible. Pitch of the

trapezoidal thread spindle 5, 10.25… in mm per revolution

Length of the linear actuator in mm

Gearbox ratio

Leadscrewpitch

:

:

Actuator length

Actuators (submenu for actuator 1-8): Activate by pressing the encoder button

rotation | : | Direction of rotation of the actuator, CW vs CCW
Park enable | : | if you activate this option the actuator will not be parked

Offset in pulses is set after calibration. And used as the lower

zero point of the actuator.

Offset from the lower zero point of the actuator as the parking position

Offset is calculated in total Global + actuator pulse speed for calibration

Pulse speed for the slow speed movement to and from the

home position

Operating speed

Value for changing the offsets

:

Cal. Offset | :
Park position | :

Calib. speed

Low speed

:

:

High speed

multiplier

:

:

17th

Formula rotating actuators

// for 24 bits
_bitmax = 0xffffff;
MaxPos =

// 16777215;
RIG . ppr * // Servo encoder positions (10000) RIG . mechanik_GearRatio_Servo /
RIG . elektrik_GearRatio_Servo /
RIG . Range factor ; // == 2 for rotating actuators

So for example:

AASD15A 10000 ppr Encoder

Gearbox 1:50

PN98 = 2

= 10000 * 50/2/2

= 125,000 positions per half round

Resolution depends on the arm length At 180

mm

Formula linear actuators

MaxPos | = ( RIG . ppr * RIG . mechanik_GearRatio_Servo / RIG . elektrik_GearRatio_Servo * ( RIG . leadscrew_length / RIG . leadscrew_pitch ));

SFX 100 type

AASD15A 10000 ppr Encoder

Gearbox 1: 1

PN98 = 2

Leadscrew = 5

Leadscrew length = 100 mm =

10000 * 1/2 * (100/5)

= 100000 positions / 100 mm

resolution = 0.001 mm

18th

SET UP
FPS LC display | : | Sets the refresh rate of the display
| | Should be 5-10. Values above 10 are not tested. Allows the
| | display to be updated in online mode. Should be off for no
| | interruptions in operation ON Servos are switched off (RIG falls
| | down) OFF Servos stop but are on.

Normaly open or normaly closed (included in next FWupdate) Normaly open

or normaly closed (included in next FWupdate)

LCD online | :
Emergency Stat | :

Online SW

Emergency SW

:

:

It is recommended to deactivate the display in game. The movement is much smoother and softer. The reason for this is that the display needs wait states and thus disrupts the interrupts for pulsing the actuators.

Edit: Has been revised and the display imperceptibly disturbs the movement. Nevertheless, the recommendation is to only leave the display activated for settings during operation.

19th

### kinematics

# Danger : WIP

For calculations of the inverse kinematics of the Stewart platform, the geometric values of the platform are stored in this menu. These are queried as follows

Basic platform: Length L1 and L2

The basis for this is a regular or irregular hexagon

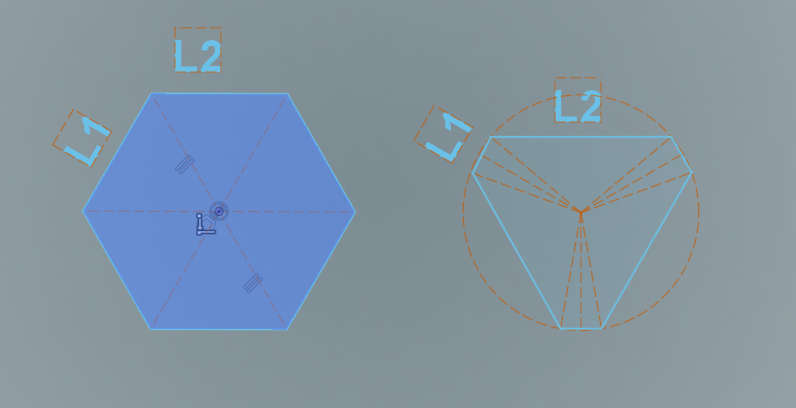
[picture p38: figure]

Fig. Left regular and right unequal hexagon

Movement platform: Length L3 and L4

The same geometric basis also applies to the upper platform (the movement platform), but here an unequal-sided hexagon is almost always used as the geometric basis. The corners of which are rotated by 60 degrees to the base.

20th

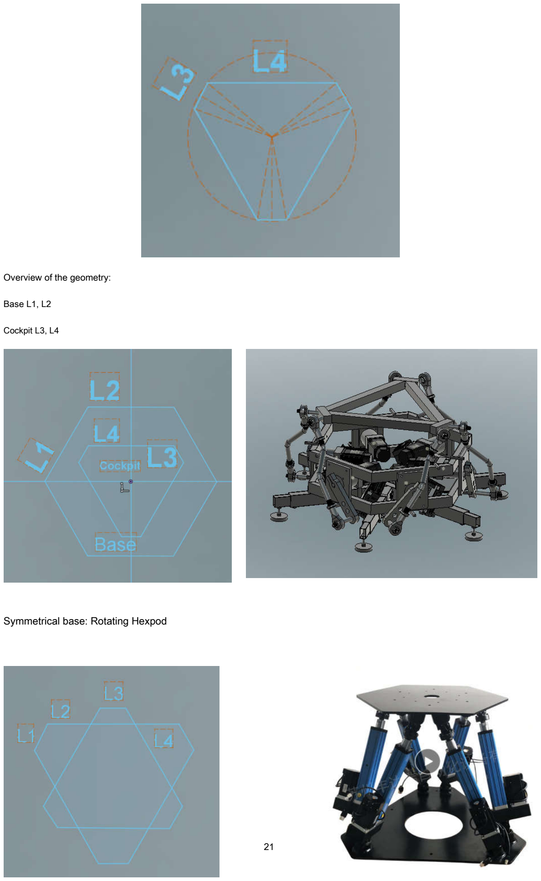
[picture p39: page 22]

Overview of the geometry:

Base L1, L2

Cockpit L3, L4

Symmetrical base: Rotating Hexpod

21

Uneven base: Linear Hexpod

For the calculations with linear actuators, you still need the total length of the actuator in the home position "Rod Length". The value of the range of the actuator is taken from the "Actuator" menu. For rotating actuators you also need the angle of the lever arms of the motors in relation to the X-axis according to the following sketch. These are stored in Crank Angel [1..6]. In addition, the length of the connecting rod "Rod Length" and the length of the lever arms "Crank" To define the home position geometrically, you also need the angle of the lever arm in the home position. This can be determined arithmetically (18 ° -29 °).

22nd

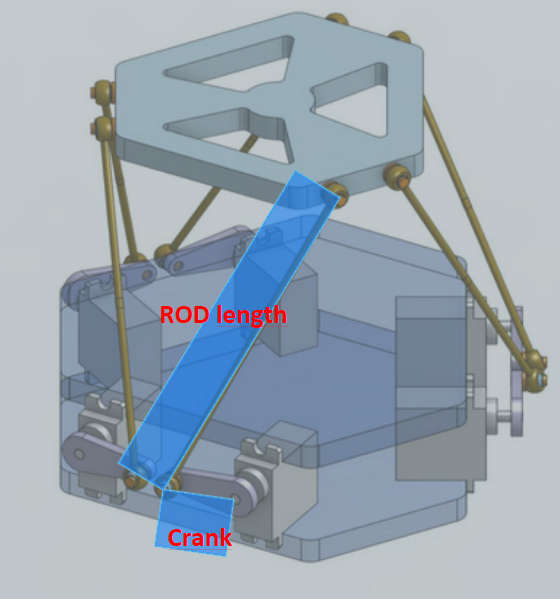
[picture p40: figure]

23

## FTDI USB interface

The controller contains an FTDI FT232 RL chip that is installed via USB.

The drivers required for this are usually installed automatically under Windows. But these can also be done via:

https://www.ftdichip.com/Drivers/VCP.htm

downloaded and installed.

## Data transfer / interface information

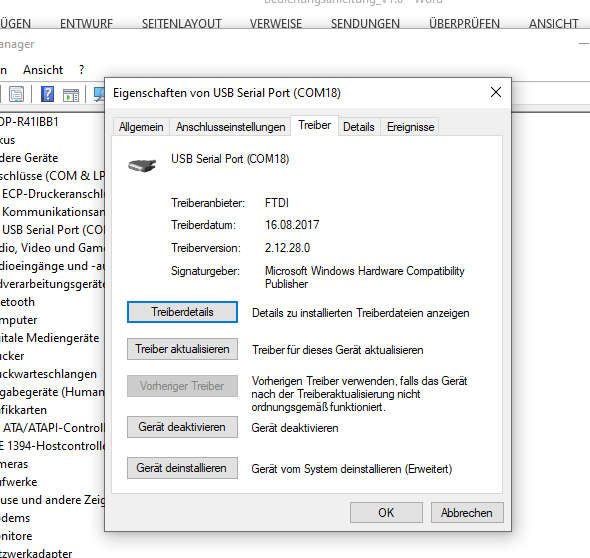
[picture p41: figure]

The data transfer is established via the standard USB interface.

The data packet string now is 28 bytes long and includes additional spare motion data slots for up to 8axis

The ID is byte values 0xFF + 0xFF Each axis is 24 bit wide.
LF + CR is required in the end (0x0A + 0x0D)

ID AXIS1 AXIS2 AXIS3 AXIS4 AXIS5 AXIS6 AXIS7 AXIS8 LF / CR

Data output
speed
Databits
Stop bits
Parity

binary
250,000 baud

### 8 bit

1
None
24

Data format

### 2 start bytes

### 24 data bytes

### 2 stop bytes

<255> <255> or for inverse kinematics <253> <253> 3 bytes (24bit) per channel / actuator 8 channels
<10> <13>

DANGER:

The start bytes <255> <255> activate the direct data mode, i.e. the positions of the actuators from Simtools or Mover are transmitted directly.
The start bytes <253> <253> activate the "inverse kinematics" here the values for inverse kinematics, i.e. acceleration, speed or position / degree, must be transferred. The values must be transferred standardized to a range. For further information see chapter "Inverse Kinematics"

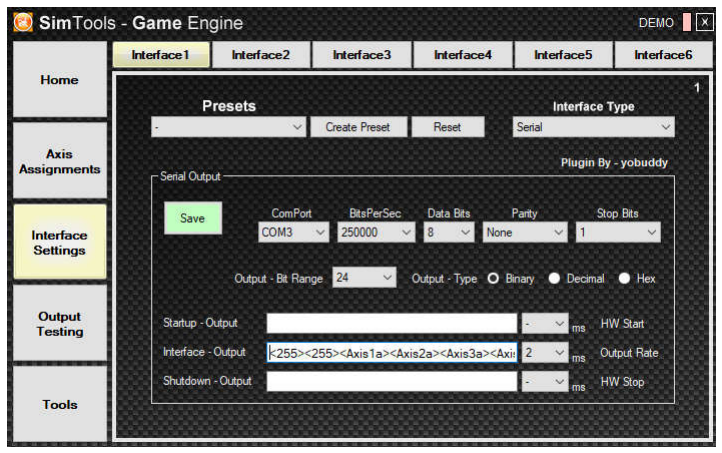
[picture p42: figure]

25th

### Kinematics menu

The entries here are recorded individually for each DOF

### 1. Surge Longitutional Movements 2. Sway Laterold Movements 3. Heave Vertical Movements

4. Yaw | Z-axis rotation angle
5. Roll | X-axis rotation angle

### 6. Pitch Y-axis rotation angle

The following settings can be made for the input values. In addition, the output filters can and are activated if set.

### 1. Gain of the input signals

### 2. Range of values (scaling to the 24-bit input)

### 3. Activate the washout effect of the axis (high-pass filter) 4. Strength of the washout effect 5. Smoothing of the input values (EMALP filter) 6. Strength of smoothing

### 7. Activate the logistics filter

### 8. Factor for the logistics filter

Danger

If you use the inverse kinematics, note the setting in your Motion Cue program (Mover / Simtools etc) there, scale the value range that you receive from Xplane for Yaw to e.g. + -24 degrees to 24 bits so that the controller knows how to evaluate the input data , please adjust the value under Range in the Axis menu. In this case the 48 would be for + -24 degrees.

26th

## Firmware update

If necessary, regular firmware updates are delivered. You can find this under

https://github.com/motion4sim/AASD15A-Servo-Controller-for-Motion- Simrigs / tree /
master / firmware

download and install on the controller according to the separate instructions. It's very easy. The update process is

explained in the following video.

https://www.youtube.com/watch?v=c0Djy7tlofE

The update instructions can also be found under

https://github.com/motion4sim/AASD15A-Servo-Controller-for-Motion-Simrigs/tree/master/user- guide

A bootloader tool is required for the update process. You can download it here

https://github.com/motion4sim/AASD15A-Servo-Controller-for-Motion- Simrigs / tree / master / bootloader

Attention: before you update the firmware you can save the data with the new remote app

You can find this app here:

https://github.com/motion4sim/AASD15A-Servo-Controller-for-Motion- Simrigs / blob /
master / remote_app /

Attention, please reset the controller to the factory settings after every firmware update.

You can find instructions on how to do this later in this document.

27

### LED display

Meaning of the ads

Green LED lights up

The red LED lights up

Green and red will light up,

green and red will flash

Controller online and receiving data

Controller offline, calibration or Moves to the parking position Moves to the

home position to wait for online data Spike filter active

### Wiring of the emergency stop switch and online switch

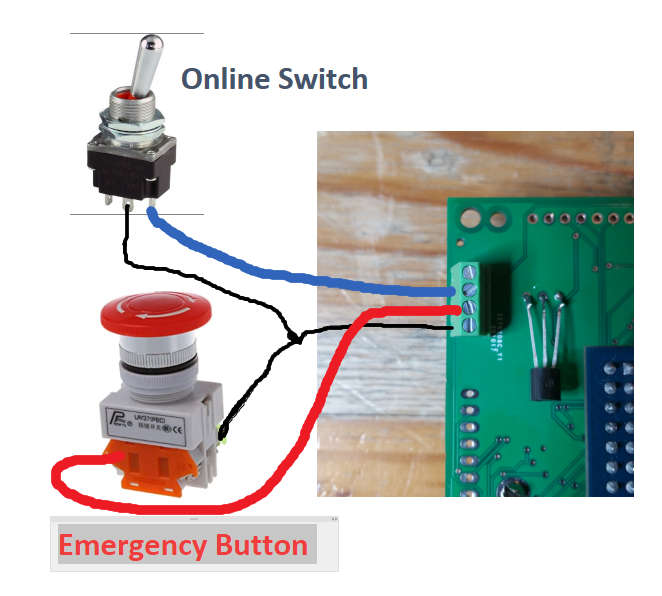
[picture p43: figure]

28

## Factory reset

Sometimes it is necessary to reset the data in the controller memory to the original state. To do this, use the following instructions

### 1. Restart the controller

### 2. Wait until the message "press encoder to calibrate ..." appears in the display

### 3. Then turn the encoder to the left to open further menu entries

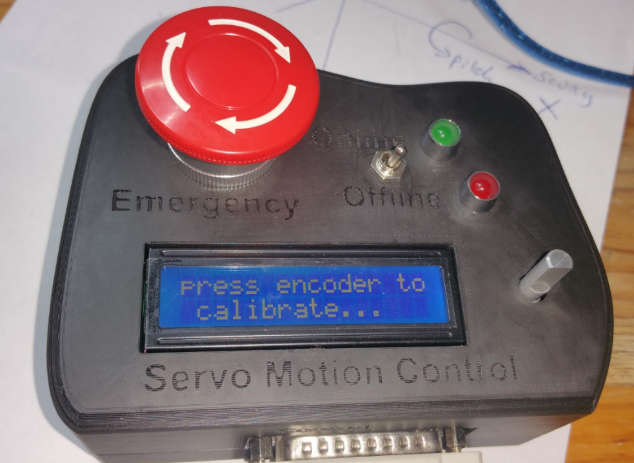
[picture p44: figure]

4. Turn until "press encoder .. factory restore" appears in the display. Press the encoder to do this.

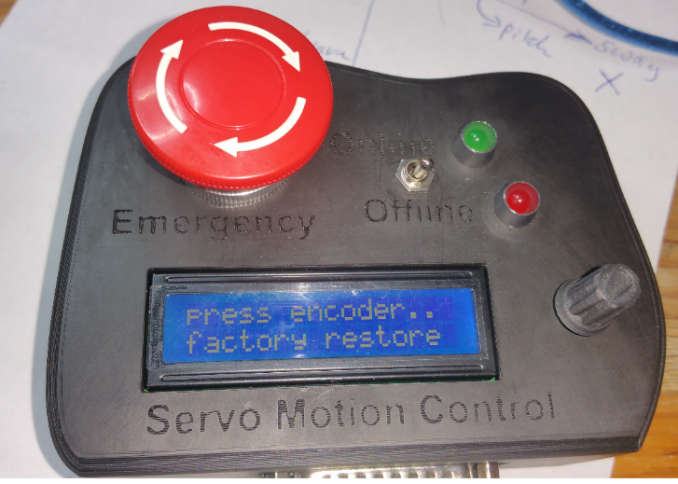
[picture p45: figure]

5. The data has been reset.

29

Connection servo 7

The 7th servomotor can optionally be connected in this way.

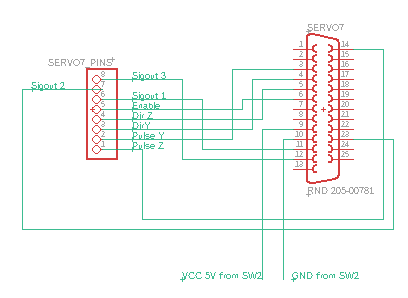
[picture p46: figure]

The Vcc 5V and GND must be shared by another connector (SW2 or display). In future PCB layout there will be 2 extra contacts for GND and VCC 5V

### NEW - Native USB Port - FW-Flash, Remote, Motion

From FW version 1.17b, the native USB port has received additional functions

The following functions are now possible through this port.

### 1. As before, firmware update of the MCU

30th

### 2. Access to the Eeprom as well as reading and writing of the controller variables

### 3. Works as a USB CDC device and also receives telemetry data for standard mode and

inverse kinematics.
4. In FLypt Mover, for example, simply set the port and set the baud rate as high as possible.

Disadvantages of motion data via this port:

Due to the software Usbstack, the execution of the pulse engine in the controller is irregularly interrupted, which leads to micro-jerking. It is possible that this feature can be eliminated in future firmwares.

### Remote APP

There is now a new smart remote APP for easy editing of the controller configuration. With this, the most important data can be downloaded from the controller, modified, saved and written back.

Download from Gitub:

https://github.com/motion4sim/AASD15A-Servo-Controller-for-Motion- Simrigs / tree / master / remote_app

To read out the data, select the appropriate COM port and click "Connect".

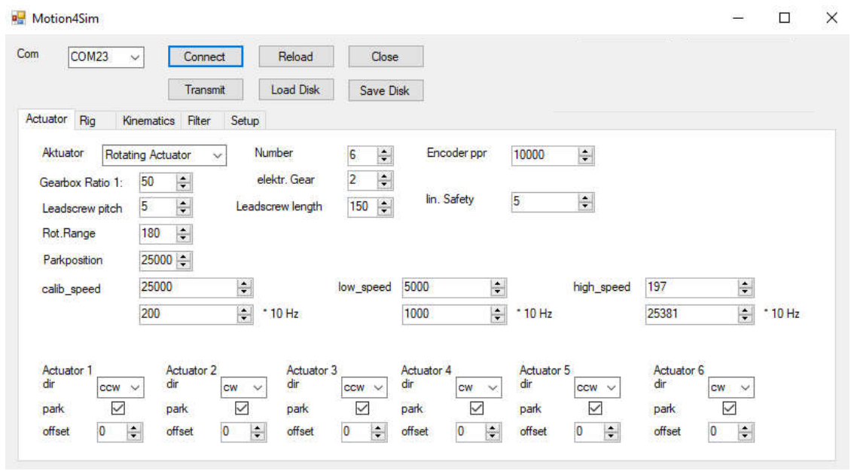
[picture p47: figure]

The other buttons are self-explanatory. To save the data back to the controller, select "Transmit". The values can be saved locally with “Load and Save Disk”.

31

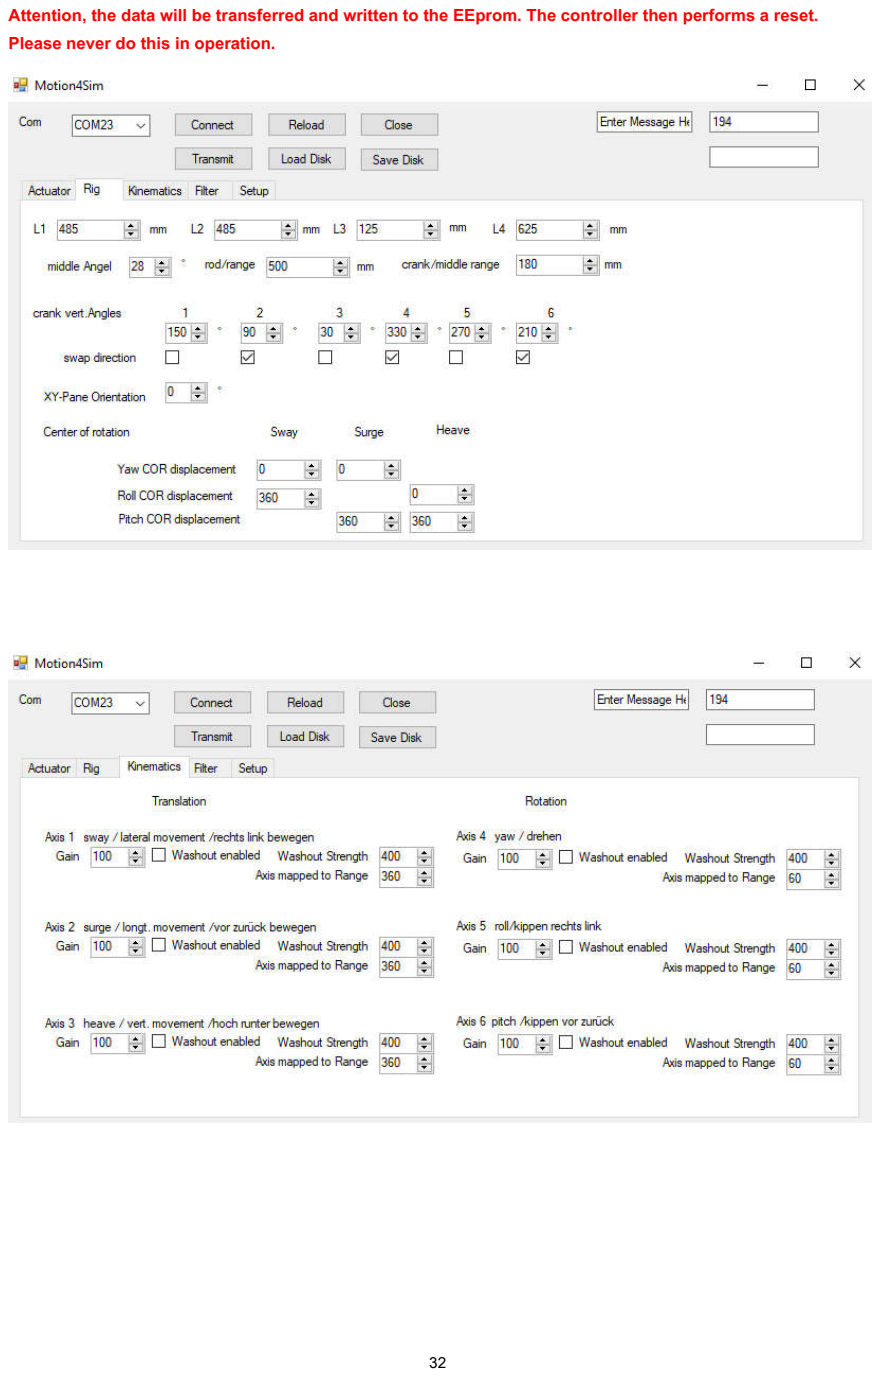
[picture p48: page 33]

Attention, the data will be transferred and written to the EEprom. The controller then performs a reset. Please never do this in operation.

32

Attention, the APP is WIP and still contains a number of errors. In addition, no plausibility check is carried out for the values entered.

33

Have fun

Motion4SIM

Braunsdorf 14.3.21

Update follows.

34

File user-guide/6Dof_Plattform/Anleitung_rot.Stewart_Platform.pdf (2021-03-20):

Anleitung Simulator

Transport:

Zum Transport, das obere Cockpit von der Stewart Plattform lösen 8x Schrauben M8 Inbus . Gewicht ca 35 kg
Die Stewart Plattform wiegt ca 105 kg. Davon die Pleuel mit den Gelenkaugen und die obere Plattform wiegen ca 25 kg
Für den weiteren Transport auch durch normale Zimmertüren empfiehlt es sich die Pleuelstangen und die obere Plattform abzubauen.
Dafür müssen die 12x M16 Muttern an den Pleuel-stangen gelöst werden(sind nur leicht angezogen). Bitte beachten sobald eine Pleuelstange entfernt wurde verkippt die obere Plattform. Diese bitte durch unterlegen von Distanzklötzen oder durch eine 3. Hand sichern.
Das Unterteil kann nun von 2 Personen getragen oder geschoben werden. Durch Türen gelangt man durch absetzen auf 2 Füßen und schieben für hochkant. Die Montage erfolgt in umgekehrter Reihenfolge. Die M16 Schrauben sind fest anzuziehen(normaler Schraubenschlüssel mit 3/4 Kraft. Diese Schraubverbindung sollte regelmäßig vor Benutzung kontrolliert werden.
Eine Wartung weiterer Bauteile ist nicht erforderlich. Die Gelenkköpfe sind selbstschmierend.(Teflon)

Kabelverbindung

1x Strom AC 230V 16A abgesichert
1x USB , Daten ,Flash und Motion(neben Netzkabel)
1x USB nur Motiondaten (neu Hochauflösend und ruckelfrei -> diesen verwenden

Es können beide Kabel an den Rechner angeschlossen werden. Sollte nur das reine Motiondaten Usbkabel benutzt werden empfiehlt es sich einen powered Hub vorzuschalten.

Für die Telemetriedaten kann Simtools oder Flyptmover verwendet werden

Simtools Einrichtung:
https://www.youtube.com/watch?v=4Fvx0h11oO0&t=3s

Flypt Mover :
Siehe Controller Manual und https://www.flyptmover.com/

Motion Profiles für Mover: https://github.com/motion4sim/AASD15A-Servo-Controller-for-Motion-Simrigs/tree/master/mover_6dof

Die Anleitung für den Motion Controller : https://github.com/motion4sim/AASD15A-Servo-Controller-for-Motion-Simrigs/tree/master/userguide

Inbetriebnahme:

1. Alle Kabel verbinden
2. Hauptschalter einschalten
3. Warten bis Controller fertig gebootet hat. Im Display steht "press Encoder to Calibrate"
4. Achtung: Nach dem drücken setzte sich das System in Bewegung und kalibriert sich.
5. Prüfen ob Not-Aus funktioniert.
Achtung: wird der Not-Aus betätigt werden die Servomotoren "kraftlos "geschalten , die Plattform fällt zu Boden.
Dafür gibt es in den Einstellungen weitere Möglichkeiten.
6. Wenn alle Aktuatoren kalibriert sind kann durch schalten des "Online Schalters" auf OFF und wieder ON das System in die StandBye Position bewegt werden. Durch schalten auf Off bewegt sich die Maschine wieder in die Park Position
7. Jetzt wird auf Telemetriedaten gewartet.

Für den sicheren Betrieb dieser Plattform ist es notwendig die Funktionsweise zu kennen. Personen sollten abstand halten. :)

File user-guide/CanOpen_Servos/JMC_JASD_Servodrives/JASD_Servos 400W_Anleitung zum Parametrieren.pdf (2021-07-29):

Hallo JMC 400 und 750W JASD - (not integrated) Benutzer!

Aus mehreren Support-Erfahrungen von und mit Benutzern mit diesem Set - JMC 400W iHSV60 und Treiber JASD 4002-20B entsteht diese Anleitung.

(Achtung: Bisher sind nur Verbindungen mit der JMC Software 1.7.6 und den jüngsten 400W Servos möglich (ab 01/2020). Die älteren 400W (bis 12/2019) und auch die aktuellen 750W Servos sind nicht per Software parametrierbar, nur per Tasten am Treiber! Bei ihnen ist auch das Oszilloskop nicht nutzbar. Ziemlich blöde Sache und, wie ich finde, ein großer und nicht verschmerzbarer Mangel bei diesen Servos.)

Die Motoren müssen zur Parametrierung eingebaut und an die Riemen/Spindeln/Mechanik angeschlossen sein. Ohne Last lässt sich kein Servo parametrieren.

Verbindung mit dem CN3 RJ45 Anschluss oder dem neueren CN5 (JASD4002 ab Jan. 2020) per micro-USB Kabel herstellen.
CN3

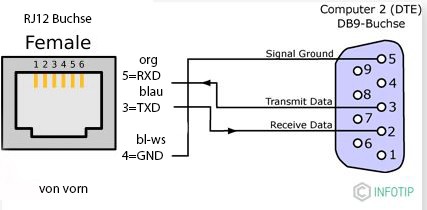
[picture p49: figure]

Oder:

CN5

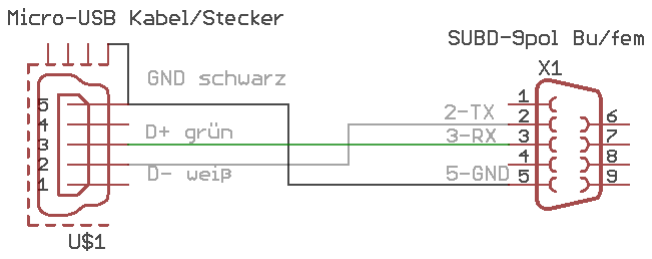
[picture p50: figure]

Die Software JMC 1.7.6 als Administrator starten, den richtigen Com-Port einstellen (über Systemsteuerung/Geräte-Manager herausfinden). Den AC Servo Motor auswählen, Turn On klicken. Auf das grüne P links oben klicken, um die Parameter zu laden. In der unteren Statuszeile müssen die meisten LEDs grün leuchten.

Das vereinfacht alles. Wenn das nicht geht, muss über die Tasten am Treiber parametriert werden. Ohne Kurven zu sehen. Dann kann man nur sehen, hören und nachmessen.
Spannend wäre, ob das Oszi bei dir funktioniert. Aber das später...

Im Prinzip ist folgendes Vorgehen sinnvoll: Motorkennwerte prüfen. In P00-xx uund auch P03-09, das sind die Encoder steps/rev - resp. microsteps/rev. Dieser Code ist nicht dokumentiert…

Dann ist der Molecule/Denominator Parameter zu ermitteln falls man eine Untersetzung hat. Formel dazu im Manual. Da sollte man nicht einfach 2:1 einstellen sondern rechnen. Und beide Parameter (P03-10 und -11) entsprechend stellen. (ich bin da echt ahnungslos, s.u.)

Den Steuer Modus wählen: P01-01 (control mode setting) bestimmt, was das Servo machen soll. Bei CNC Achsenantrieb auf Positioning, also P01-01 auf 0 stellen. Alles andere sind spezielle Anwendungen wie Fräs-Spindelbetrieb u.a.

Das Autotuning:
Autotuning einschalten: P01-02 auf 1 wäre Standard, auf 3 =30% (was immer das heißt) empfiehlt Sebastian End, soll besser sein. (Experimentierfreudige können auch mal Mode 2 - Automatic Adjustment of Rigidity ausprobieren)
Erforderlich ist, jetzt noch einen Rigid (Steifigkeits-) Parameter vorzugeben, mit dem der Automatic Adj. Mode startet. Das ist P01-03. Der geht bis 32, und man fängt mal mit 13 o. 15 an. Über 19 ist bisher keiner gekommen… P01-04 auf 0,5 stellen. Und dann die Schleife fahren (s.u.).

Der Automatik Adjustment Mode regelt die Parameter, hier sind dann keine Änderungen möglich, so lange man im Autotuning ist.
P02-00, | 1st gain of Position control
P02-01, | 2nd gain of Position control (smoothing)
P02-03, | Velocity feed forward gain
P02-04, | Velocity feed forward smoothing constant
dann noch
P02-10, | 1st gain of velocity loop
P02-11 | 1st Velocity integral constant
P02-13, | 2nd gain of velocity loop
P02-14, | 2nd Velocity integral constant

Das Oszilloskop: (in V.1.7.6)
Wenn man die Software erfolgreich verbinden konnte, kann man das Oszi einrichten und starten und während der Schleife im Oszi beobachten, ob die Pos Instruction (bit) und Position feedback (bit) Kurven nahe beieinander liegen. Dann statt Pos. feedback den Schleppfehler (position follow error) in den Ch.2 dazu holen. Start und Stop Button sind wohl klar.
Dämlicherweise kann man als drittes weder den Follow error noch den feedback auswählen. Versteht man nicht. Wer hat sich das ausgedacht? Immerhin kann man mit Pos. Instruction und Pos. follow error gut sehen was los ist. Und was sich ändert wenn man Parameter ändert.

Dann muss man mit den Div Settings spielen – ich hatte zB mit meinem 180W Servo auf dem Tisch Amplituden, wo ich 5000 bei div einstellen musste, um die Kurve vollständig zu sehen. Andere mussten 20.000 bis 75.000 einstellen. Stellt man alle Kurven gleich ein, sieht man den Fehler im Verhältnis. Man will aber optimieren, also beim Pos. following Error so viel oder wenig Div einstellen dass man auch diese Kurve vollständig sehen kann.
Bias ist die Verschiebung der Kurven horizontal. Das kann man brauchen wenn wegen hoher Div‘s die Kurven nach oben hin wandern. Ich hab für Pos. Instruction gelb, für und für Pos. feedback grün gewählt. Leider kann man bei diesem Oszi nicht alle drei gleichzeitig einstellen. Am sinnvollsten ist also die Kombination Pos Instruction und Pos Follow error.
(Der Schleppfehler ist das Wichtigste überhaupt, ein kleiner Schleppfehler führt zu runden Kreisen, eckigen Ecken und präziser Kurvenfahrt. Ein zu großer Schleppfehler macht Ellipsen aus Kreisen, runde Ecken und Abweichungen bei kurvigen Abschnitten. )

Das Ziel ist, mit der Parametrierung die Kurve Pos Follow Error so schmal und so niedrig wie möglich zu bekommen. Das kann mit der Position Loop schon gelingen, meist muss man aber die Velocity Loops dazu nehmen.

Jetzt fährt man eine Schleife von meinetwegen 100-200mm Weg hin und her, abrupter Wechsel, ziemlich schnell, so 5-6000 mm/Min. ZB 10 mal. Die Rampe sollte um die 2000 mm/s sein (Mach3/4). Dabei beobachten ob es Geräusche gibt, Knarren, Quietschen, Pfeifen. Dann schwingt schon was. (Klopfen kann allerdings auch ein Symptom von zu wenig Verstärkung sein...) (Langsamer gefahren ist die Regelung lahmer und schlechter. Wir wollen eine "Sprungantwort" erzwingen, die in gewisser Weise die Qualität und Wirkung der Regelung zeigt.)

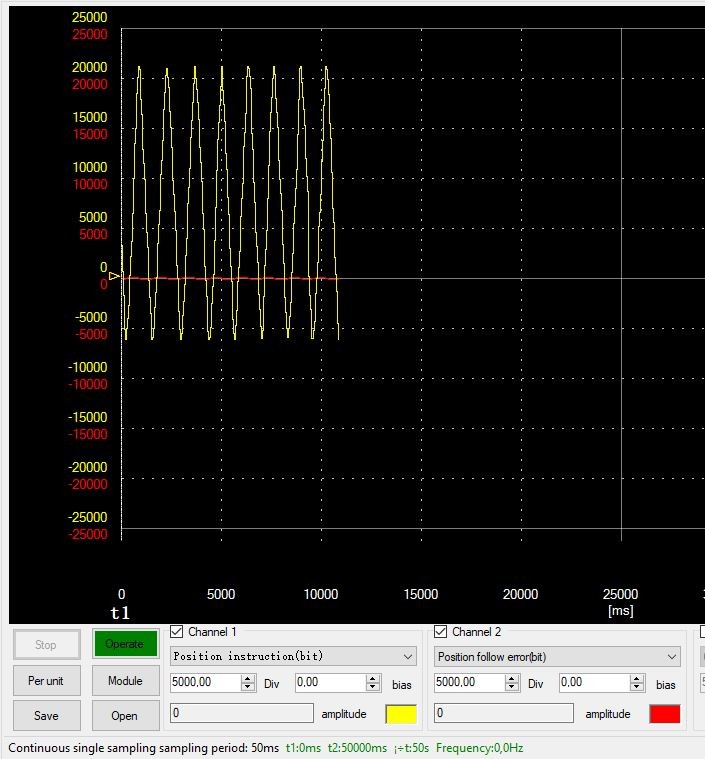
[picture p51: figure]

(Hier im Bild läuft ein
Servo ohne Last,
Schleppfehler in rot,
minimal)

Hier ein Beispielcode:
#Gcode für eine Testschleife x100F6000

x0F6000
x100F6000
x0F6000
x100F6000
x0F6000
x100F6000
x0F6000
x100F6000
x0F6000
x100F6000
x0F6000
x100F6000
x0F6000 usw

Also - wenn du diese ersten Werte vom Autotuning hast und dir alles noch zu weich vorkommt, gehst du mit -P01-03 (Steifigkeit) jeweils einen Wert höher. Wieder Schleife und begucken. Teste die Steifigkeit, indem du versuchst von außen die Achse zu bewegen. Wenn das um mehr als 0,1mm gelingt, bzw sich die Spindel verdrehen läßt, weiter Steifigkeit erhöhen. Ich sag mal, 19-20 wäre Maximum. Wenn es bis dahin nicht steif genug ist, muss man manuell ran und gezielt die Gains justieren. Parallel dazu immer im Oszi den Schleppfehler beobachten. Wird er größer, liegt man mit der letzten Einstellung eher falsch.

Das war jetzt die Grundeinstellung mit Autotuning. Einschalten und Steifigkeitsfaktor.
Wenn dir das schon steif und gut genug ist, lass es so stehen. Jetzt gehts um die letzten 25%. Wir sind noch nicht fertig 🙂

Nun die Werte für P02-00, 02-01, 02-03, 02-04, auch P02-10 und-11 und -13 und -14 in einer Tabelle notieren. Dies sind die Startwerte für das manuelle Tuning.

Manuelles Tuning:
Dazu das Autotuning abschalten - P01-02 auf 0 stellen.
P02-00, -01, -03, -04, P02-10, P02-11, können nun manuell justiert werden.
(So wie ich die Parameter der 400W Serie lese, gibt es einen P und einen Geschwindigkeits-Regler (Velocity Loop, ab P02-12) . Der P-Regler hat einen P und V Anteil und der V - Regler nur eine Loop- und Verstärkungsregelung. Kann man als I-Regler deuten. Eine D-Regelung ist hier nicht zu sehen. (Doch: die Pseudo-differenzial Feedforward Gains P02-12 und-15. An denen hab ich noch nicht experimentiert. Prinzipiell würde man die erhöhen, wenn man eine super schnelle Regelungsreaktion auf plötzliche Veränderungen haben will. ZB sehr viele Richtungswechsel, Dateien mit extrem vielen spitzen Konturen.) Aber was weiß ich schon...Ingenieure bitte kommentieren! )

Der P-Anteil des P-Reglers:
(Der Proportionalanteil des Positions-Reglers - Hier wird die Regeldifferenz zw. Soll- und Istwert ausgeregelt. Der Proportionalregler kann den Sollwert aber nie komplett erreichen, weswegen die Gains einen bestimmten Wert hinzufügen, um dem Sollwert möglichst nahe zu kommen)
Die Positioning Gains P02-00 und -01 sollten als erstes nacheinander manuell justiert werden. Immer die gleiche Abfolge: höher stellen, bis die Regelung schwingt, dann 10-20% zurück. Nächstes Gain. Bei beiden kann man ruhig größere Schritte machen, zB 50 weiter. (ein Erfahrungswert lag um 700 für P02-00 und um 600 bei p02-01 , bei einer anderen Maschine bei 1050 und 1100) also - nichts ist "richtig". Diese Werte sind individuell für jede Maschine!

Die Erhöhung dieser beiden Pos. Werte kann schon völlig ausreichen um die erwünschte Steifigkeit zu erreichen. Dabei auch wieder den Schleppfehler im Oszi der Software beobachten!
An dieser Stelle mal einen Screenshot vom Oszi Bild erstellen. Und Werte notieren.

Der Geschwindigkeits-Anteil des P-Reglers:
(Hier wird das Integral der verbleibenden Regeldifferenz genutzt, um den Sollwert möglichst schnell und genau zu erreichen.)
Bei P02-03 und -04 wäre ich vorsichtiger, die Werte zu erhöhen. Sie erhöhen die Geschwindigkeitsverstärkung bzw -04 glättet/dämpft diese. Sprich Dynamik. Kann man machen, muss man evtl. sogar für den Schleppfehler - aber bitte mit aller Vorsicht. Höchstens 10er Veränderungen… und ebenfalls zurückdrehen, sobald es schwingt. Oder wenn der Schleppfehler wieder ansteigt.

(P02-04, der Velocity Gain Dämfungs/Glättungswert) hat eine interessante Nebenwirkung, die ein Freund beim „Spielen“ herausfand: je niedriger der Wert, umso stärker fährt die Achse Untermaß, je höher, desto stärker wird die Soll-Pos. überfahren) – ist irgendwie logisch, denn wir spielen hier mit dem I-Anteil, der ja immer was „drauflegt“.
An dieser Stelle erneut einen Screenshot vom Oszi Bild erstellen. Und die erreichten Werte notieren.
Die Geschwindigkeits-Schleife:
(Ab P02-10 gibt es Einstellungen für die Geschwindigkeits-Schleife. Auch hier geht es um den zusätzlichen Geschwindigkeitsanteil, der zur proportionalen Positionsregelung hinzugefügt wird, um eine besonders genaue und schnelle Annäherung an den Sollwert zu erreichen.)
P02-10 wird vom anfänglichen Autotuning erkannt. Range 0-2000 Hz – So hoch einstellen wie möglich, aber es steigt das Risiko von Schwingungen, Rauschen und abruptem Lauf bzw Stopps. (Gefährdung der Mechanik!) Da kann man auch aufhören wenn man fühlt dass es die Maschine zerreißt :)
P02-11 dämpft diesen Effekt, Mutige können also die -10 schön hoch drehen und mit -11 so weit dämpfen dass es gerade noch nicht zu hart für die Mechanik ist. Ich erinnere mich aber, dass Sebastian End mit zu harten Einstellungen seine Kugelumlaufmutter zerlegt hatte.

P02-12 und -15 erst einmal auf dem mit dem AT ermitteltem Wert stehen lassen. (...„je niedriger umso geringer die Dynamik, aber weniger anfällig für niederfrequente Störungen. Je höher, desto stärkere Dynamik, aber auch anfälliger für nf-Störungen“.) Dieser Parameter ist ein Pseudo-differentieller Parameter, der sozusagen vorausschauend die Geschwindigkeit erhöht, um schnelle Änderungen auszuführen. Er erhöht nicht direkt die Dynamik, hilft aber, die Regelung schneller zu machen für schnelle Instruction-Änderungen.

P02-13 und 14 sind weitere, sekundäre Verstärkungsparameter für die Geschwindigkeits Loop. bei Erhöhung kann man die Dynamik weiter steigern (Soll-Wert wird noch schneller erreicht) es steigt aber naturgemäß auch die Gefahr von Schwingungen. Also Erhöhung dieser Werte in aller Vorsicht sprich dezent in kleinen Schritten.
Generell – die Konstanten (=Dämpfungsfaktoren) besser stehen lassen, Veränderungen mit den Gains erzielen.

Man sieht also hierbei – die Parameter treten ab P02-00 in Paaren auf. Der erste ist ein Verstärkungsfaktor, der zweite ein Dämpfungsfaktor. Wenn man das durchschaut wird es etwas klarer mit den Werten.

Auch in der Geschwindigkeits-Schleife den Schleppfehler im Oszi der Software beobachten! Wenn der größer wird bei der Einstellerei, ist die Richtung der Veränderung falsch.

Alle anderen Parameter würde ich nicht ohne Not verstellen, außer man weiß genau, was man da tut. (Die Tabelle die ich oben empfahl, könnte sich als nützlich erweisen, wenn man dort jede Änderung und die entsprechende Auswirkung auf das Verhalten festhält. Ein bisschen Systematik schadet nicht...vor allem, wenn man nach 1 Jahr was ändern möchte)

Erfahrungen beim Parametrier-Prozeß:
Wir starten ja mit den Einstellungen aus dem Autotuning. Dabei kann es sein, dass die automatisch ermittelten Velocity Werte zu hoch sind und man mit den Position Loop Werten nicht hoch genug kommt, weil frühzeitig Schwingungen einsetzen. Dann ist es ein guter Weg, für P02-03, -04, P02-10, P02-11, -13, -14 wieder die Standardwerte einzusetzen.

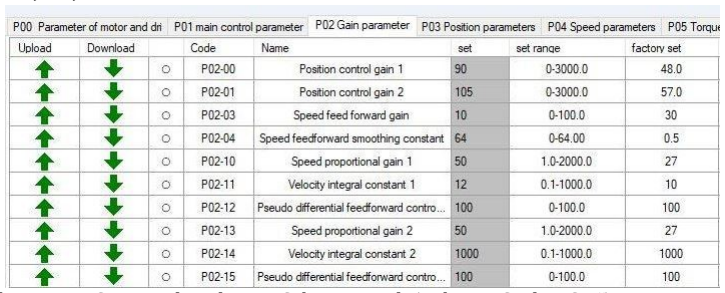
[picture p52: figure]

Nicht die Factory Sets, sondern die von Sebastian End: (stehen in Spalte „Set“)
Dann erneut die Position Loop einstellen bis zur Schwingungsgrenze, dann die Velocity und die second Velocity Gains.

Was noch?
Die Parameter in Reiterkarte P04 und P05 sind die speziellen Werte für den Speed- oder Torque Mode, die uns hier nicht interessieren und auch im Positioning Mode keine Änderung bewirken. P06 behandelt Werte die für die digitalen Eingänge bestimmt sind. Werden auch in unserem Fall nicht benötigt. Ebenso P08.
Bei den Aux-Parametern (ab S. 49) finden sich noch ein paar interessante Funktionen, u.a die Factory Restore Funktion 8 AF_ini oder die Versionsanzeige 10 AF_uEr.

Wenn man etwas Entscheidendes an der Maschine ändert, zb eine neue schwerere Spindel montiert oder sonstwie die Masse von Portal oder Zachse ändert, ändert sich ja der Wert des „Moment of Inertia) das Trägheitsmoment. Dann wäre es notwendig, die Parametrierung, mit dem Autotuning angefangen (welches den M.o.Inertia ermittelt) erneut durchzuführen, um ein optimales Regelungsergebnis zu bekommen. Das bitte im Hinterkopf behalten!

PS. Dies ist immer noch eine rudimentäre und eher praxisorientierte Anleitung, um überhaupt und rasch zu einem Ergebnis zu kommen. Ich erspare mir und Euch eine Abhandlung der Regelungstechnik, die dahinter steht und die den P-I-D Regler im Einzelnen bzw im Zusammenwirken beschreibt.
Dazu gibt es ganz gute YouTube Videos, zB von DerNormio, https://www.youtube.com/watch?v=ErOtVYJNmDU&t=52s (https://www.youtube.com/watch?v=ErOtVYJNmDU&t=52s) (Teil 3 und 7, die leider nur auf die V.5.xx ausgerichtet sind) oder Academy Raddy (https://www.youtube.com/watch?v=x0TN9Nle_dk) - völlig losgelöst von Servos, aber gut verständlich, was das Ganze soll.

So viel von mir. Bestimmt gibt es dazu Anmerkungen, Erweiterungen, Erfahrungswerte, Korrekturen und was immer für Kommentare. Die sind erwünscht und willkommen. Ich wollte mangels IRGENDEINER Start-Anleitung mal was schreiben, was bisher bei 4 Kollegen zum Erfolg geführt hat. Ja, besser geht immer…
Also bitte - gern was Erhellendes dazu schreiben, ich werde das dann einarbeiten und ergänzen.

Insbesondere die Erklärung des Molecule (Nominator) – Denominator Teils. Hab ich ehrlich nicht verstanden… was muss man für 2:1 einstellen?

PS: Das Servo-Tool von Robert Budde (https://github.com/robert-budde/iHSV-Servo-Tool) funktioniert bisher leider nur mit den 180W Servos von JMC, Version 5.xx und 6.xx.

miffysx

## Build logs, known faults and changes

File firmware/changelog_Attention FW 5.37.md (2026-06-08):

Motion4Sim M4S Controller Firmware

starting new pcb revision 3.xx with STM32 MCU

Attention  !!!!!!

latest 5.37 is only for boards shipped from 2026 !!!!

for earlier boards latest fw is 4.41 (atmel mcu boards)

## v5.37-hotfix — 2026-06-08

- fixed wrong spikefilter switch on/off or query

## v5.37 — 2026-06-02

> ⚠️ **IMPORTANT — READ BEFORE FLASHING**
>
> This firmware update also installs a **new bootloader** and a **new governor firmware**.
>
> **DO NOT unplug the board from USB power until it has fully rebooted after flashing.**
> After the flash completes, the board automatically installs the new bootloader during the first reboot.
> If you disconnect power before this process has finished, the board may fail to start and
> will need to be returned to factory for recovery.

---

### Summary

v5.37 is a significant release focused on three areas: a fully modular brake subsystem, a redesigned governor communication protocol, and a series of stability and correctness fixes across PWM, EtherCAT homing, motion filtering, and the TWI/I²C driver.

---

### Brake System — Modularisation
- Brake logic extracted into a dedicated module
- Added cold-start initialisation and HoldPower brake-engage on motion-exit
- Brake release now properly synchronised with the governor delay
- Hot-plug handling simplified: every reconnect triggers a full re-init
- refactored with clean hot-plug detection
- Belt-disable and brake interaction corrected

### Governor Protocol
- New compact **17-byte binary protocol** with sequence counter, flags, CRC-16/ARC, and reset-resume logic (replaces previous ad-hoc format)
- Added 49-byte extended read for debug-log download from the governor
- Added debug trace on brake-status changes

### TWI / I²C Driver
- Full refactor of the TWI driver
- I²C speed is now configurable at runtime

### Motion Filter
- Filter modes converted to an enum; external `OFF` is no longer permitted directly
- Soft-limiter is now optional per configuration (NEW FILTER)
- Internal filter calculations promoted to `double` precision (1 ms motion cycle)

### EtherCAT
- Limit-switch homing via DI1 implemented
- DIO debug logger added
- Brake configuration is now explicit in the EtherCAT application layer

### PWM / DMA
- `PWM_SetFrequency`: fixed skip logic, division-by-zero guard, and slot boundary check
- **Adaptive Pulsing** introduced — replaces the legacy block-pulse routine with a fully DMA-driven implementation, now also working correctly with `pn98 = 1`

  Previously, all pulses within a 1 ms cycle were fired as a block — the only approach technically possible on older hardware. With Adaptive Pulsing, a frame buffer distributes the pulses evenly across the full 1 ms window using MDMA. This means the servo experiences significantly fewer micro-accelerations and decelerations and instead moves continuously. The improvement is most noticeable during slow movements, making this a meaningful motion quality upgrade especially for flight simulation.
  NOTE: for activating adaptive Pulsing use the Checkbox in the Setup Tab
  -> this only effects STEP/DIR pulsing not for EC drives.

### Belt / Actuator
- Fixed belt park direction
- Fixed belt running direction when going offline

Version v5.36

- Web dashboard now also available on the second LAN interface (W5500 Ethernet Controller port)
- Added **mDNS (Multicast DNS / .local hostname resolution)** support for easier network access
- type motion4sim.local in your browser to enter the dashboard, works only on systems supporting mDNS
- Introduced **Belt Torque Mode** for Actuator 7 and AASD servos (using analog 0–10 V control) *PRO feature*
- Improved  park position handling in the EtherCAD system: optimized motor standstill detection with increased tolerance
- Added extended configuration options for the Online button:
  * Normally Closed (Latching)
  * Normally Closed (Momentary)
  * Normally Open (Latching & Momentary)
- Various minor fixes, adjustments, and dashboard improvements

- Web Dashboard now public on the github:
       https://github.com/motion4sim/motion4web-dashboard
- Note: Web Dashboard uses external motion4sim server , you can setup your own server and config 
        the url in the network section of the Dashboard.
	Web Dashboard is http only !! allow mixed use in the browser
	is Work in Progress use with care	

Version v4.41

- Bugfix for RIC numbers: resolved sporadic incorrect “curved” homing behavior
- Added extended configuration options for the Online button:
  * Normally Closed (Latching & Momentary)
  * Normally Open (Latching & Momentary)
- added long Button press feature triggers shutdown for momentary buttons
- Improved shutdown functionality, aligned with STM firmware implementations

Version v5.35

- note update takes 3-4 minutes
- added new rigtypes 
- factory reset linear is now vnm geometry and settings
- factory rest rotational is now mk3 settings
- added mxp rigtypes
- improved shutdown function for actuators  incl backoff factors
- added token activation support for pro & pro+ boards (no online needed)
- repaired actuator check for step/dir interface
- added  rs485 support
- small release bugfixes
- bootloader fw update, ethernet fw update
- governor fw update

Version v5.34   Attention not compatible with older boards , pcb must be > rev 3.xx !!!!!

- complete new code for stm mcu
- starting with all the features from 4.40
- adding 2nd Wind channel
- added native ethercat support for A6 servos
- added support for 2nd LAN w5500
- added WebServer for WebDashboard for native LAN w5500 will follow
-> motion4sim.local where local is supported

Atmel Boards -> for pcb revision 2.xx 

Version v4.40 compatibility update

- change cfg datasystem to cbor for compatibility to new Dashboard system
- everything else remains

Version v4.30

- added PWM Output for Pin Extra02 to use with WIND
- added Wind Support for Channel 8 
   Direct Mode 
   -> use 0x00 is PWM 0% Duty  and  0xffffff 100% Duty (24bit Values)
   Positionmode
   -> use 0x00 is PWM 0% Duty  and  0xffffffff 100% Duty (32bit Values)
- For using PWM with 4Pin PWM Fans Connect Extra02 to PWM Signal and GND to 12V FAN GND
- added other Functions for Extra02 to choose with Dashboard Setup Config
  or Controller Setup Menu
   ->Servo ON Indicator
   ->Homing Switch
 - please Note the Wind is for Pro Boards only atm.

Version v4.29

- fixed some GMAC problems
- fixed EEPROM corruption, 
-> added  crc check for config and a 2nd dataset, factory reset in case of corruption
-> please not when updating to this fw you will get a corruptionwarning at 1th start!!
-> needs a data transmit or factory reset to protect the data from now
-> update shows "eeprom corrupted" only push encoder to continue and perform factory reset
- added USB authentication with Dashboard for pro boards
- fixed some LWIP stuff (memory leaks and controller stuck), mainly DHCP and double packets
- fixed bugs in eth hotplug

Version v.4.27 fix 1

- fixed belt homing direction
- change network missing message not show any more

Version v4.27

- added Settings menu entry in StartMenu
- added Motion Operation Menu (old Menu) and splitted the entry in settings and motionoption
- fixed bug in jitter correction from  fw 4.23 or dont know
- fixed bug for pcb1.xx when return from motion operation and actuator check , thanks @greg for support
- fixed brake clipping randomly thanks @motionbasti for helping testing
- several code optimizing binary size shrinked a lot
- changed cw/ccw definition internal 
  ->note: - dashboard config files saved are wrong now for motion direction! edit them or make a new copy !!! 
	  - also Dashboard preset(saved in config files) also have now opposite cw/ccw values !!	
	  - factory reset is working!
- officially only pcb from v1.09 are supported with fw >4.xx now

Version v4.26

- fixed igpm timers not reporting correctly for multicast
- added ethernet shutoff when using usb transfer
- added eth hotplug disabled while online
- speedup ethernet bootup and auth for new boards
- added ip showing up in prestart menu when using pro
- changed wtg configuration while startup
- improved i2c smart handheld integration

Version v4.25 fix1

- added RGB LCD support
- fixed usb stuttering while getting to many Ethernet packets

Version v4.25

- added belt torgue mode support for actuator 7
- added I2C Handheld support
- renew timer and event system
- added basic hotplug support for ethernet
- renew transitions for motion
- new motiondata timeout activates transition when data the same > 2 seconds
- added Demomode(rig configured for positionmode)
- changed speeds for homing belt
- watchdog improvement , but can still occure sometimes while booting up and init
of ethernet needs longer
- smaller bugfixes 

Version v4.24

- added m4s  & mxp license system to activate the pro features
- removed lots of bugs for compatibility to old boards (4.1 & 4.22)
- fw factory reset needed
- also download and install latest Dashboard 
- please note old dashboard profiles will setup network not correct, create new profile
  from factory reset

Version v4.22

- bugs from 4.10 repaired

Version v4.10

- added Ethernet UDP,HTTP support for pcb v2.03
- added I2C support for pcb v2.03 for new Handhelds ,EEPROM and Crypto ID, 
- added SPI support for pcb 2.03 SPI Displays/Handhelds
- preparation for RGB LCD support for new Handhelds and Onboards pcb 2.03

- added Watchdog support
- removed bug in homing algorithm
- removed bug in positionmode causing small spikes

- new prestart menu with more options
- added mcu temp watch
- no reboots when transmit config to board (testing)
- repaired shutdown -> ends in prestartmenu
- fixed several usb communications freezes in serveral menus

pay attention test safely before use some part are total new rewrites.

fw is mainly tested on boards from pcb v 1.09 older may work but !
try on your own risc!!

Version v3.32 fix2

- fixed broken motion usb port from fix1
- almost stable reported
- it keeps as testing because i have 2 weeks no rig to test finally

Version v3.32 fix1

- fixed online bt setup when using dashboard for config
- limit mastergain in factory setting to 100%
- fixed go online after homing command

Version v3.32
- factory reset required after flashing!!!
- added support for latching and fixed Online switch Buttons .. only in controller Setup Menu
- hwpulsing now always activ when supported, pcb version >1.08 
- pcb version < 1.09 not guaranteed to work correctly because of software pulsing
- major changes to pulse engine
- doubled pulse & inverse kinematics rate from 500/s to 1000/s
- also filters calculation rate now from 2ms to 1ms  -> filter behaviour may change adjust values
- removed usb data timing jitter complete

Version v3.30

- factory reset required after flashing!!!
- added Actuator Input Data matrix, 
- so you can use SRS or Simtools Actuator order without reconnecting cables
- edit via Handheld in Actuators menu or use Dashboard in Filter tab
- only for direct mode!
- in position mode you will need still clockwise actuator connection starting with 1 at front left actuator 
- fixed shutdown function torque recognition and not rebooting
- fixed service menu torque recognition

Version 3.29

- added separate fifo for usb motion and data
- in principle, both USB ports can be operated in parallel
  need to test what happens when Motion data is received on both ports
  so be carefull using it
- changed debouncing for killswitch and online switch
- improvement of serial pattern detection
- added SimHub  support

Version 3.28 

- added message crc datachecks to all communication 
- the end chars 0x0a 0x0d are replaced with crc16 checksumm
- still back compatible to 0x0a 0x0d if send to recieve but sends only with crc so older dashboard will not recieve data
- update to Dashboard Version 3.28
- works only full with Dashboard >=v3.28 because crc checks
- fixed motionusb port problems

Version 3.26

- just for testing fw updates with flypt

Version 3.25 fix1

- fixed  short brake release impulse when startup with EM Button engaged
- fixed  online speed set to 50khz only in some conditions

Version 3.25 

- hardware pulsing is stable now ,just enable, works same, read advice in dashboard
- small change to break release delaytiming
- new spike algorithm is now implemented 
	-> adjust spikwindow for setup from smaller value to higher
	-> read also fw3.15 release note down this list
- old spike is emalp+spike2 option now in filter setting
- changed lowspeed in factory settings
- changed breakdelay to 100ms in factory settings
- @dureiken changed factory setting motionxp for spike to spike2 and cal/lowspeed settings
- no changes to dashboard made same version 

Version 3.24 

- a lot of changes test your rig behaviour before pratical use!!
- added new EM Button debouncing with Software and Hardware
- added prompt ">" for Setup and Configuration values
- fixed flashport at startup wrong config  data transmission 
- added transition to standby with special triple emalp filtering, 
	-> also into motion from standby uses now this transition
	-> setup transition speed for this its in seconds
- maybe for better transition adjust the low speed to 5000*10hz in setup (Speed from/to Standby Position)
	-> this also changes auto homeing speed for belt
- hardcoded service speed set to 1000x10hz before was low speed too
- extra01 pin is now low at startup in case for brake nc use
- controller firmware reset, now only possible in save rig states
- dashboard controls "transmit"  accepted only when restart/offline phase possible
- fixing service menu emergency issues
- changed doubleclick recognition speed a little bit faster 
- fixed belt spike2 problem (no spike calculation for belt)
- removed doubleclick feature in the menu

Version 3.20

-  removed motionsystem introduced in 3.10 -> done by Dashboard now
-  added support for flash-usb port for motion and dashboard use
-> i recommend this port now for all operations
-  added hw pulsing support for pcb version from 1.09 (could double resolution)
-  added option for inoffz. srs supp with native usbport mod
-  added support for new motioncueingsystem included in dashboard now
-  this fw operates only with dashboard version 3.20 
-  added realtime belt retreat modification 
-  added adjust.servobrake switching delay

Version 3.15 

- lcd init problems fixed everything else seems to emi related
- lcd only comes to garbled char when workhour timer is active (normaly deactivated)
- option in menu -> setup -> Mastergain enabl : if set to off Mastergain is fixed on main screen
- long press (>3s) of encoder button does a lcd screen init
- double click feature for encoder button
	-> fast double click switches main screen from 
		gain"100%" -> "Sp Win" Spike Window -> "Belt" retreat -> "Filter" Emalp value back to gain
	-> you can change value with encoder turning left or right
	-> values were not saved to eeprom
	-> for saving go to menu "Save and return"
	-> with double click you can also leave any menu back to main screen with no saving
- new Spike Filter design
	
	defined with 3 Values.
	
		Menu -> Filter 	-> Spike Filter 	
				-> Spike Window
				-> Sp.Filter smooth

	-> Spike Window:  from 1...400% (or more) 100%  is 1/4 actuator range in pulses
    	 	-this means if pulse input is more than say 100% (1/4 of actuator stroke) Spike is detected
		-pulsestrain is cut/limited to Spike window size pulsecount
	-> Spike Filter: 
 		- after Spike detection the Emalp(normal Filter) raises every frame(2ms) Spikestrength value is lowpass over raising emalp	
		-> this means lower value faster growing Filter (after spike slower return to normal motion)
		-> higher value ,lower growing filter ( after spike faster return to normal motion)
	-> Sp. Filter smooth:  when spike is finished (pulsetrain smaller as Spike Window)
		-> dyn Emalp filter decreases(2ms) with  Sp.Filter smooth ( Emalp over decr. value) 
		-> this means higher value slower decrease and slower return to normal motion
		-> and vice versa
	
	//for me follwing values have worked
	//Spikestrength = 20 to 80  (higher means more smooth in spike)
	//Spikewindow from 10%  for racing 20-40 % for flying  (higher means later spike detection)
	//Spike smooth 2-10   (higher means longer of spike smoothing ,do not use 1 never ending spike) 

Version 3.11 release

continueing lcd fixes
watch also 3.10 notice
- long press (5s) of encoder button does a lcd screen init

Version 3.10 release

Pay attention Motioncueingsystem is W.I.P. start with low scale first
Factory Reset is important for Motioncueingsystem to work
please install also latest Dashboard v3.10 for full use of Motioncueingsystem

-added full scripting motioncueing and filtersystem
-added autotuning system to scale the motioncueing profiles
-added system for storing motionprofiles in flash
-added doubleclick feautre for inputsystem
-added function to boot intobootloader in setup menu
-added support for new pcbversion 1.09 hardwaretimers

Version 2.23 release

- added dashboard support for belt configuration
- added working hour meter reset support ( press user button > 15 seconds for reset)
- lcd working now with no problems
- this fw support only until pcb v. 1.08
- last fw for this boards
- some code improvements

Version 2.19 release

- added belt actuator support
- added new emergency mode "keep online"
- added extra01 function send timer signal
- added sineloop for testing actuators
- added working hour meter
- factory reset needed from fw 2.11
- fixed most lcd problems but still not all yet :(
- better code perfomance
- cleanup 

Version 2.11

- added  support for SFX 3 actor  System in position mode
- no factory reset needed
- fixed homing issue with linear systems other then 6dof
- lcd garbage issue still exist _ screen reinit time now is shorter

Version 2.01

-complete rewrite of the motion engine
-now best motion ever 
-some smaler bugfixes (Service Menu)
-led blinking in some states
-code cleanup
-rewrite of serial port code
-rewrite of lcd display routines
-no srs support :)
Attention - for older first series boards there is also necessary to update the bootloader, contact me for this !!!

Version 1.60 Factory reset needed !! storage  changed

- included SFX RIG types in kinematics calculation BETA!
- activatet Native USB Port to work with Dashboard APP and Motiondata ->still not good as it should use MotionData port
- improved interface to Dashboard App
- load and Install also new Dashboard App

Version 1.54

- serial data interface  transfer extended for new Dashboard App
- works only with new DasBoard App correct,please update
- always do a factory reset after flash
- some bugfixes, linear factory reset, and 6dof float mode
- fixed srs

Version 1.51

Attention:	Factory reset needed !! storage  changed

- rewrite of service actuator moving functions
- usersettings moved to internal MCU flash storage  -> factory reset needed ! 
- factory reset possible with on board button (press 4 seconds for rotating Act setting and 8 seconds for linear Act settings)  
- stability of usb for apps improved
- update also to latest apps

Version 1.47

Attention: 	- eeprom data changed  _ after flashing do factory reset !

- fixed some servo7 bugs
- fixed linear actuator safety bug (safety >pitch)
- added function for servobrakes WIP
- added new transition to motion
- added adjustable time for transition to motion
- added offset for linear actuators
- added adjustable Online Position
- added adjustable Maximum Gain
- better actuator check function (also while homing)
- added shutdown function (drives actuators down to homing point and powers servos off; turn left in menu ) 
- smaller changes in menu texts
- some value checks added
- most new settings only from handheld adjustable actually

thanks to Dirty for testing

Version 1.42

Attention: 	- eeprom data changed  _ after flashing do factory reset !
		- save your settings to paper!! remote App changed data completely
		- install new Handheld app version
		- install new config app version

- added fully support for servo 7 ( remove some resistors on board before use)
- added support for infinite actuators
- bug fix of version 1.41_fix1 display stuck after flash
- some bugs fixed in srs autoconnect
- smaller changes in menu texts
- fixed bugs with remote handheld app
- changed actuator check function 

Version 1.41

-added interface for remote handheld app at native usb port
  (u have to wire the native usb port)
- minor code changes
- spikefilter led keeps on bug fixed
- transmit data from app doesnt reboot  fixed
- memory protection feauture inkluded
- updated bootloader for automatic software bootloadermode ( board delivered later as 062821)

Version 1.30

- added few remote commands for remote app testing features
- now fw has support for Sim Racing Studio in amcsd15a mode
- changed filter timing 
- minor bugfixes and code changes

Version 1.20

Attention: 	- eeprom data changed  _ after flashing do factory reset !
		- save your settings to paper remote App changed data completely

- complete new actuator settings, each actuator can be different , special for linear rigs seatmover
- keys and buttons using interrupts now
- native usb port on same70 board only for fw update
- remote app works now only with motion data port on breakout port
- remote app new version release for this firmware
- lcd fps setting now working
- new option for encoder direction

Version 1.19

- new data mode for floating point values from flypt mover
- changed some  motion cueing calculation for linear actuators
- improved 3d calculation to support center of rotation 
- fixed emergency button problems
- factory reset available for linear and rotating actuators
- remote app some minor changes
- fixed bug loading factory data when using remote app before calibrating

Version 1.18

- remote app expanded ,for now function only to native usb port
- native usb port and ftdi usb port working together now
- native usb port not for motiondata due to usb stack problems with pulse engine
- some changes to onboard motion cueing  now xyz koordsystem works like flypt
- motion cueing with linear 6dof rig works thanks to [GER]Basti-Discord

Version 1.17 Beta

- new usb remote configuration interface
- simple gui app  on github
- please check plattform after transmit configuration data controller will reset

Version  1.16 Beta

- change LCD - Display Init
- usb cdc code for target usb port (near ethernet connector) support asyn. cdc transfer
- enter bootloader via emergency-bt online-sw encoder-bt pressed and power on
- modified calculation of rotat. and linear inverse kinematics

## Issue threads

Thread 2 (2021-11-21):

How to contact you?

HUANGJIN169, 2021-11-21:
Hello, how can I contact you? Can I leave a message to get your contact information? Or Facebook.

motion4sim, 2021-11-23:
 

Hi, you can contact me with email

here ***@***.***

or you connect to me via discord

motion4sim#4206

How may i help you?

Thank you

b.regards motion4sim

ps: i dont use meta services

Gesendet: Sonntag, 21. November 2021 um 15:55 Uhr
Von: "huangjin" ***@***.***>
An: "motion4sim/AASD15A-Servo-Controller-for-Motion-Simrigs" ***@***.***>
Cc: "Subscribed" ***@***.***>
Betreff: [motion4sim/AASD15A-Servo-Controller-for-Motion-Simrigs] How to contact you? (Issue #2)

Hello, how can I contact you? Can I leave a message to get your contact information? Or Facebook.

—
You are receiving this because you are subscribed to this thread.
Reply to this email directly, view it on GitHub, or unsubscribe.
Triage notifications on the go with GitHub Mobile for iOS or Android.

Closed 2021-11-24.

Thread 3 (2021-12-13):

Feature suggestion: Add park position functionality for linear actuators

Dirt-e, 2021-12-13:
Hey @motion4sim,

Super high-quality real-time motion controller you made there! Lovin' it!

I've got a feature suggestion:
Whenever I flip the switch to "Online" my linear actators smoothly run up to the park position (50% position) and then my software takes over from there. Thing is, I would like this takeover to take place in the 0% position already.

Would it be possible to allow a "Park Position" parameter to be set in the controller for linear actuators as well? Analogous to how it's  handled on rotary actuators?

Cheerst,... Dirty :-)

motion4sim, 2022-06-17:
function included now

Closed 2022-06-17.

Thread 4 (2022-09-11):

About PCB

1248280302, 2022-09-11:
How do I get the control board and servo driven PCB.I didn't find it

motion4sim, 2022-09-11:
Hi you can order  direct from me call me on discord
motion4sim#4206  or email me motion4sim@gmx.de

or use

https://www.tindie.com/stores/motion4sim/

https://eu.sim-motion.com/produkt/motion4sim-servo-motion-controller/

https://www.ebay.de/itm/255366595618

https://www.etsy.com/listing/1251559353/m4s-motion-controller-sim-racing-sfx

HUANGJIN169, 2023-07-30:
Many people told me that some of the links you bought above are invalid.
 Then I tell them to contact your email
  I help you promote in Facebook group

motion4sim, 2023-07-31:
thank you
i will update
https://www.ebay.de/itm/256069012332

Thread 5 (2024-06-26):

Is this suport 4 corner actuactor, withsurge and 2 TL rear and front?

artayasa, 2024-06-26:
Is this suport 4 corner actuactor, withsurge and 2 TL rear and front?
I want to used simhub motion.
And it suport step/dir??
Iam planing to try first with stepper motor. Bacause iam project make diy servo drive with step/dir interface.

motion4sim, 2024-06-26:
Hi, the board can handle 7 motors , if you need more you can use 2 boards in parallel.

simhub support is in development and ready in the next time. it supports step dir.

checkout our discord: @motion4sim

artayasa, 2024-06-26:
> you can use 2 boards in parallel.

What do u mean pararel sir??.
Okee i will try with step/dir on stepper, need to add limit switch for homing ??

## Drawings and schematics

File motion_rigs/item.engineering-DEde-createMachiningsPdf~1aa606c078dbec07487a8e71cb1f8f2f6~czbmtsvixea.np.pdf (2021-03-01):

# Projektübersicht

## Projektname: 2021-02-24 Engineering Project

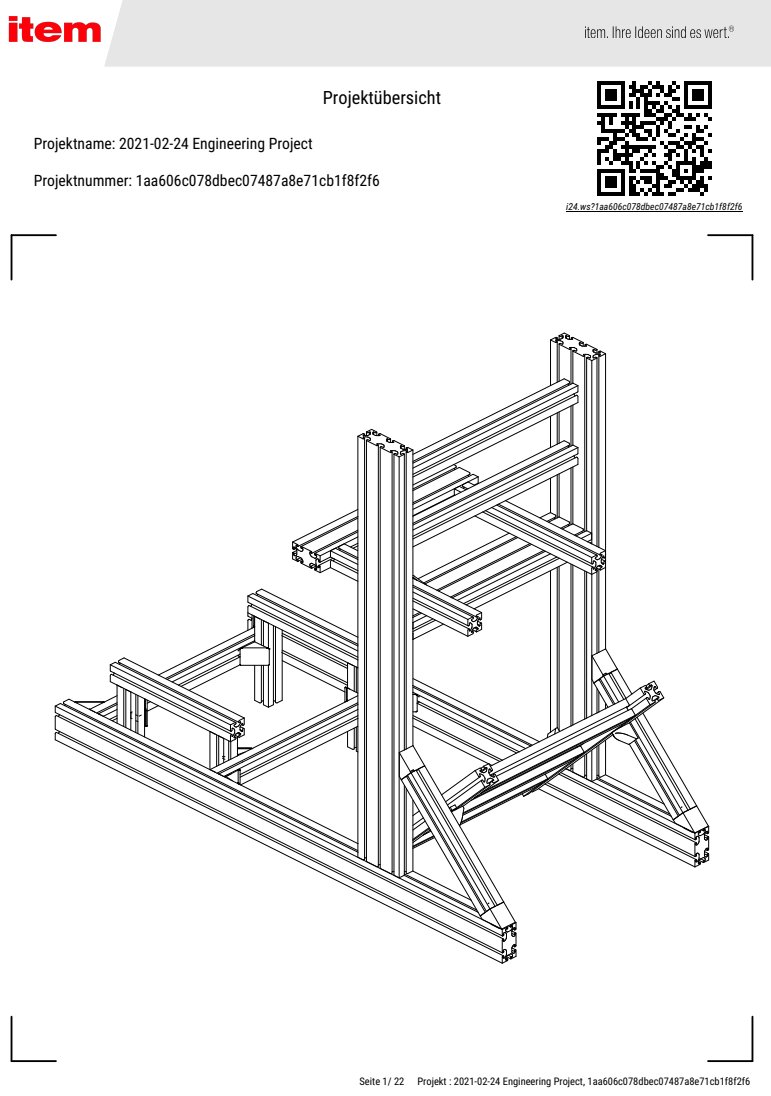
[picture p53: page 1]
Projektnummer: 1aa606c078dbec07487a8e71cb1f8f2f6; i24.ws?1aa606c078dbec07487a8e71cb1f8f2f6

Seite 1/ 22 Projekt : 2021-02-24 Engineering Project, 1aa606c078dbec07487a8e71cb1f8f2f6

# Baugruppenübersicht

## Baugruppe 1

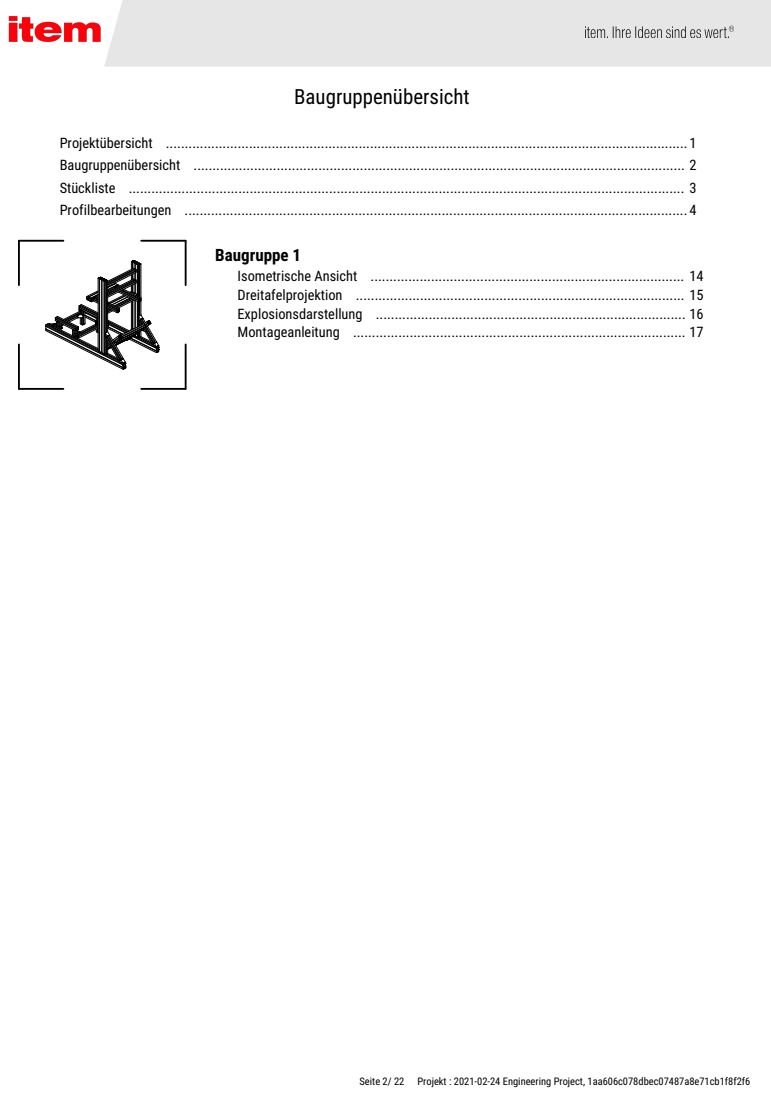
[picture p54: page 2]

Seite 2/ 22 Projekt : 2021-02-24 Engineering Project, 1aa606c078dbec07487a8e71cb1f8f2f6

# Stückliste

Position | Artikelbezeichnung | Artikel-Nr. | Seite | Anzahl

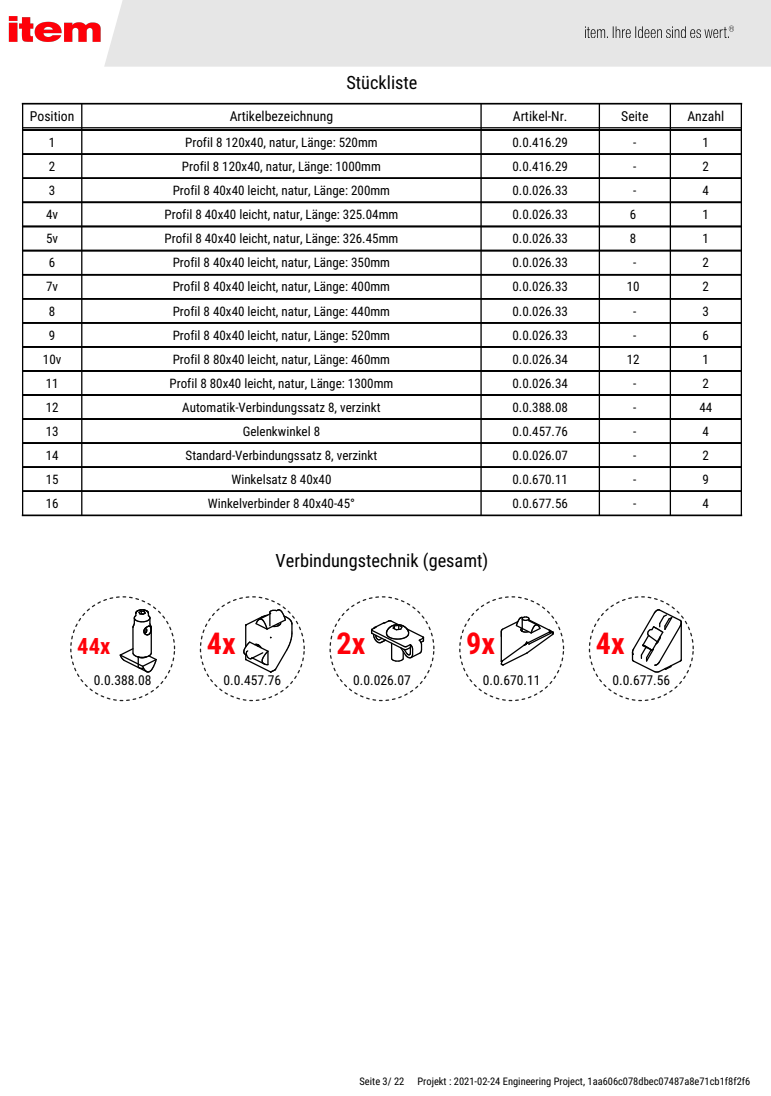
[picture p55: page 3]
Verbindungstechnik (gesamt)

1 | Profil 8 120x40, natur, Länge: 520mm | 0.0.416.29 | - | 1
2 | Profil 8 120x40, natur, Länge: 1000mm | 0.0.416.29 | - | 2
3 | Profil 8 40x40 leicht, natur, Länge: 200mm | 0.0.026.33 | - | 4
4v | Profil 8 40x40 leicht, natur, Länge: 325.04mm | 0.0.026.33 | 6 | 1
5v | Profil 8 40x40 leicht, natur, Länge: 326.45mm | 0.0.026.33 | 8 | 1
6 | Profil 8 40x40 leicht, natur, Länge: 350mm | 0.0.026.33 | - | 2
7v | Profil 8 40x40 leicht, natur, Länge: 400mm | 0.0.026.33 | 10 | 2
8 | Profil 8 40x40 leicht, natur, Länge: 440mm | 0.0.026.33 | - | 3
9 | Profil 8 40x40 leicht, natur, Länge: 520mm | 0.0.026.33 | - | 6
10v | Profil 8 80x40 leicht, natur, Länge: 460mm | 0.0.026.34 | 12 | 1
11 | Profil 8 80x40 leicht, natur, Länge: 1300mm | 0.0.026.34 | - | 2
12 | Automatik-Verbindungssatz 8, verzinkt | 0.0.388.08 | - | 44
13 | Gelenkwinkel 8 | 0.0.457.76 | - | 4
14 | Standard-Verbindungssatz 8, verzinkt | 0.0.026.07 | - | 2
15 | Winkelsatz 8 40x40 | 0.0.670.11 | - | 9
16 | Winkelverbinder 8 40x40-45° | 0.0.677.56 | - | 4

Seite 3/ 22 Projekt : 2021-02-24 Engineering Project, 1aa606c078dbec07487a8e71cb1f8f2f6

# Unbearbeitete Profile

## Teil 1, Profil 8 120x40, natur

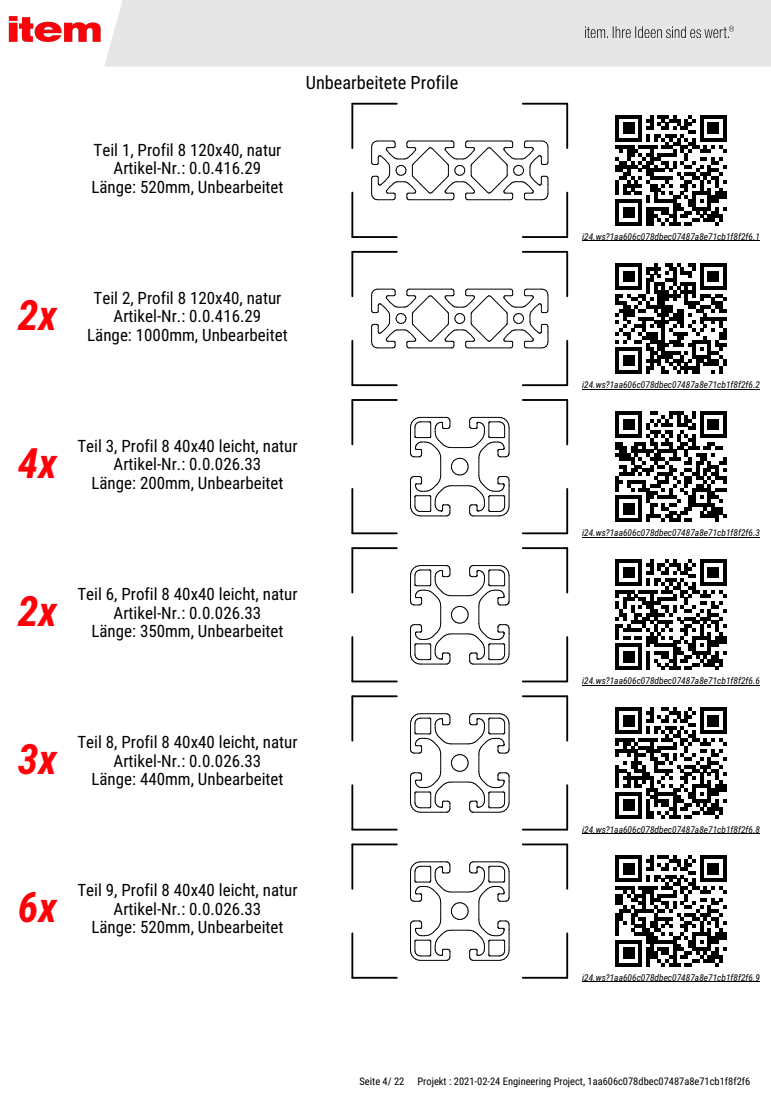
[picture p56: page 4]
Artikel-Nr.: 0.0.416.29 Länge: 520mm, Unbearbeitet; i24.ws?1aa606c078dbec07487a8e71cb1f8f2f6.1; Länge: 1000mm, Unbearbeitet 2x; i24.ws?1aa606c078dbec07487a8e71cb1f8f2f6.2; Länge: 200mm, Unbearbeitet 4x; i24.ws?1aa606c078dbec07487a8e71cb1f8f2f6.3; Länge: 350mm, Unbearbeitet 2x; i24.ws?1aa606c078dbec07487a8e71cb1f8f2f6.6; Länge: 440mm, Unbearbeitet 3x; i24.ws?1aa606c078dbec07487a8e71cb1f8f2f6.8; Länge: 520mm, Unbearbeitet 6x; i24.ws?1aa606c078dbec07487a8e71cb1f8f2f6.9

Teil 2, Profil 8 120x40, natur
Artikel-Nr.: 0.0.416.29

Teil 3, Profil 8 40x40 leicht, natur
Artikel-Nr.: 0.0.026.33

Teil 6, Profil 8 40x40 leicht, natur

Teil 8, Profil 8 40x40 leicht, natur

Teil 9, Profil 8 40x40 leicht, natur

Seite 4/ 22 Projekt : 2021-02-24 Engineering Project, 1aa606c078dbec07487a8e71cb1f8f2f6

# Unbearbeitete Profile

## Teil 11, Profil 8 80x40 leicht, natur

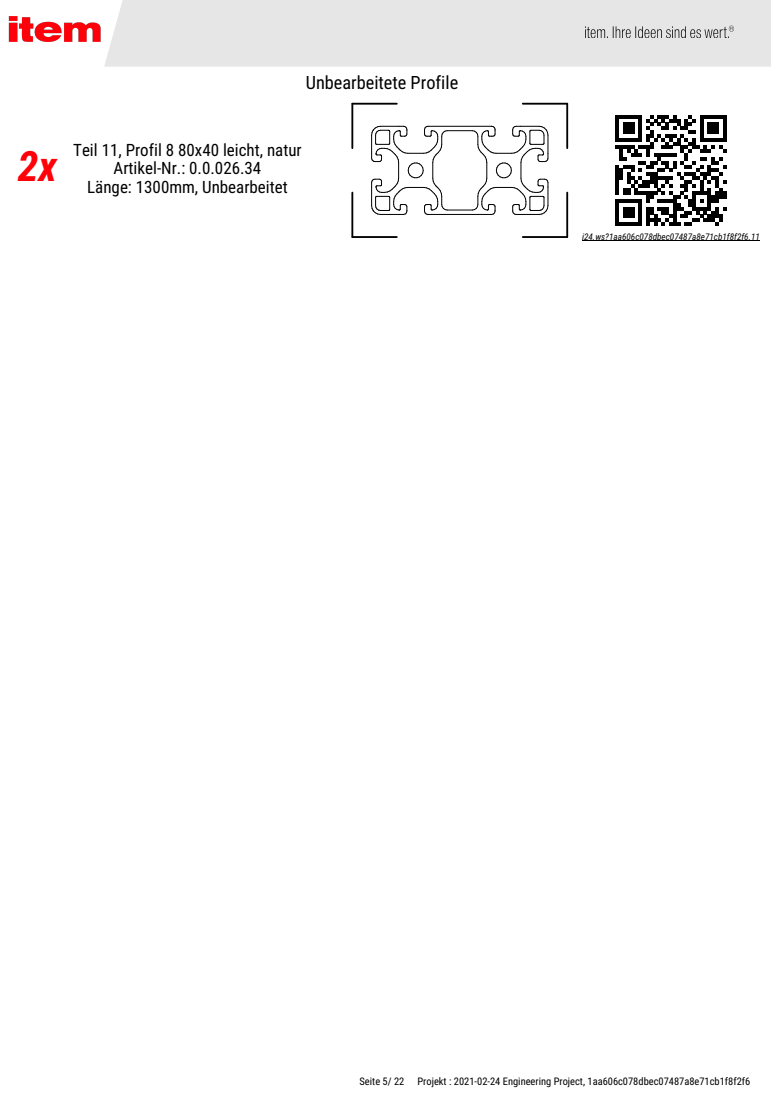
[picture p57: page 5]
Artikel-Nr.: 0.0.026.34; Länge: 1300mm, Unbearbeitet 2x; i24.ws?1aa606c078dbec07487a8e71cb1f8f2f6.11

Seite 5/ 22 Projekt : 2021-02-24 Engineering Project, 1aa606c078dbec07487a8e71cb1f8f2f6

# Bearbeitungen Teil 4v, Profil 8 40x40 leicht, natur Artikel-Nr.: 0.0.026.33, Länge: 325.038mm

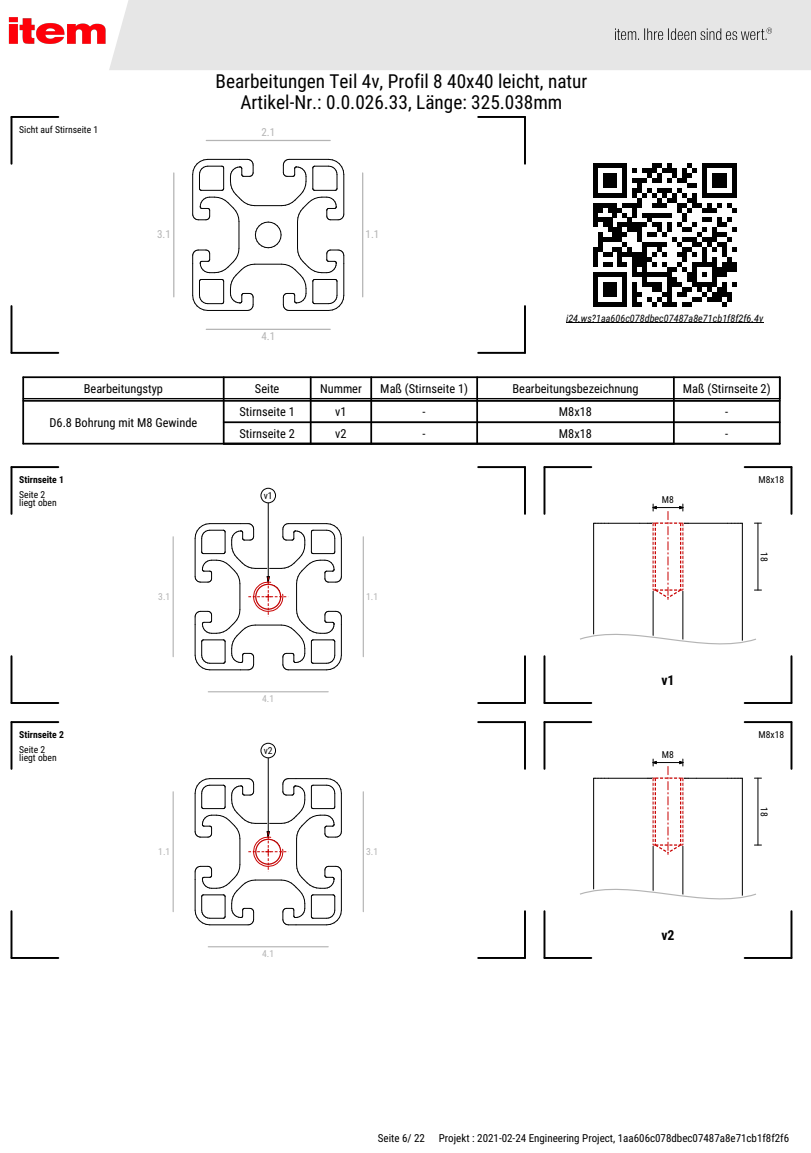
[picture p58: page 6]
i24.ws?1aa606c078dbec07487a8e71cb1f8f2f6.4v; Stirnseite 1; Seite 2; v1 liegt oben; Stirnseite 2; v2 liegt oben

Sicht auf Stirnseite 1

Bearbeitungstyp | Seite | Nummer | Maß (Stirnseite 1) | Bearbeitungsbezeichnung | Maß (Stirnseite 2)
D6.8 Bohrung mit M8 Gewinde | Stirnseite 1 | v1 | - | M8x18 | -

Stirnseite 2 | v2 | - | M8x18 | -

Seite 6/ 22 Projekt : 2021-02-24 Engineering Project, 1aa606c078dbec07487a8e71cb1f8f2f6

# Kontrollansicht (Bearbeitungen) Teil 4v

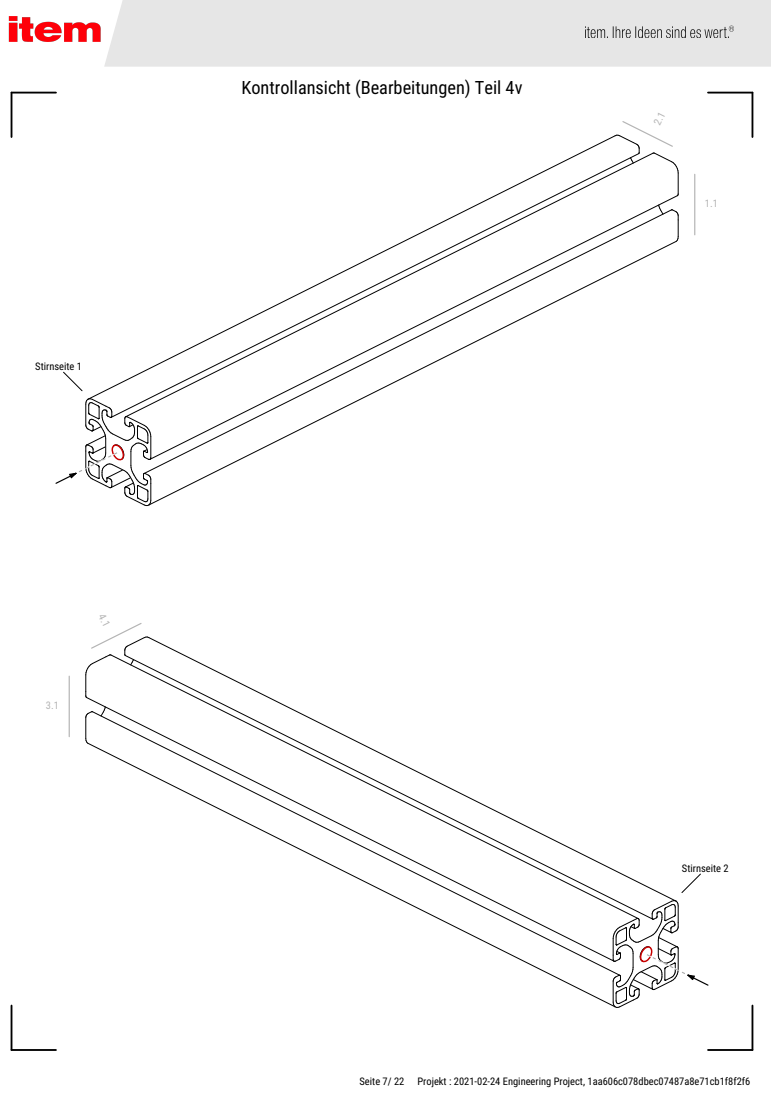
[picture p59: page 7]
Stirnseite 1; Stirnseite 2

Seite 7/ 22 Projekt : 2021-02-24 Engineering Project, 1aa606c078dbec07487a8e71cb1f8f2f6

# Bearbeitungen Teil 5v, Profil 8 40x40 leicht, natur Artikel-Nr.: 0.0.026.33, Länge: 326.452mm

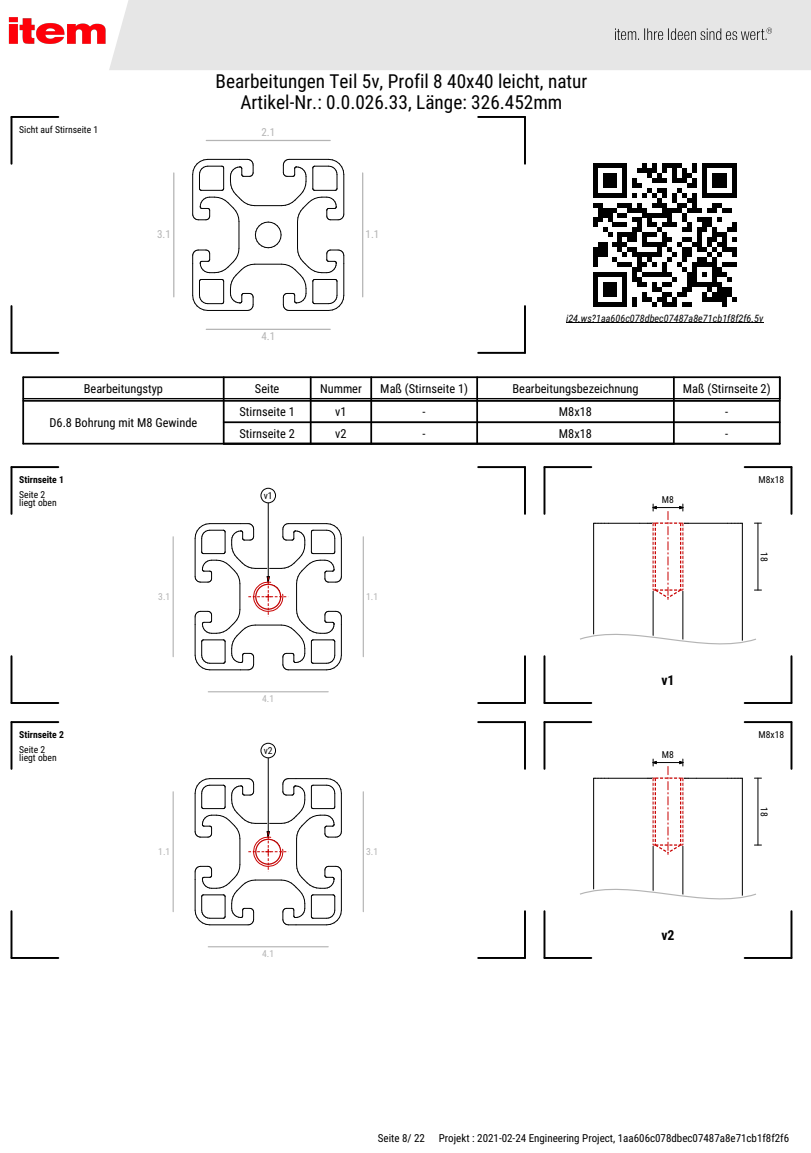
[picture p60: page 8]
i24.ws?1aa606c078dbec07487a8e71cb1f8f2f6.5v; Stirnseite 1; Seite 2; v1 liegt oben; Stirnseite 2; v2 liegt oben

Sicht auf Stirnseite 1

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

Stirnseite 2 | v2 | - | M8x18 | -

Seite 8/ 22 Projekt : 2021-02-24 Engineering Project, 1aa606c078dbec07487a8e71cb1f8f2f6
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

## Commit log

2020-11-20 update 2
    [Controller_case_oben_lcd_enc_v4.stl, Controller_case_oben_v12.stl, Controller_case_unten_lcd_enc_v4.stl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]
2021-03-04 fw 1.17b update
    [factory_settings_m4s_rotating.cfg]
2021-03-14 release fw 1.18
    [factory_settings_m4s_rotating.cfg]
2021-07-29 update all
    [scop.xls]
2021-10-06 update 3d files
    [Controller_case_oben_lcd_enc_v4.stl, Controller_case_oben_lcd_enc_v5.stl, Controller_case_unten_lcd_enc_v4.stl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]
2022-03-08 update 080322
    [factory_settings_m4s_linear.cfg, factory_settings_m4s_rotating.cfg]
2022-06-17 update
    fw update
    [Controller_case_oben_lcd_enc_v5.stl, Controller_case_oben_v12.stl, Controller_case_unten_lcd_enc_v5.stl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]
2022-07-31 update
    update dashboard files
    [Controller_case_oben_lcd_enc_v1_04.stl, Controller_case_oben_lcd_enc_v5.stl, Controller_case_oben_v12.stl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]
2022-08-11 update
    update fw 2.11 and dashboard 2.16
    [factory_settings_m4s_linear.cfg, factory_settings_m4s_rotating.cfg]
2023-06-09 Update FW & Dashboard
    [pcb_case_1.07_mysimkit_bottom.stl, pcb_case_mysimkit_down_v1.09.stl, pcb_case_mysimkit_top_v1.09.stl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]
2024-01-27 update 3dprint
    [gehäuse_down_pcb_v1110_display.stl, gehäuse_top_pcb_v1.10_display.stl, pcb_case_1.07_mysimkit_bottom.stl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]
2025-01-31 fw update 4.25
    [factory_settings_m4s_linear.cfg, factory_settings_m4s_rotating.cfg]
2025-12-03 Simhub
    www
    [pcb_case_display_bottom_motion4sim_v203.stl, pcb_case_display_top_motion4sim_v203.stl, rotary_knob_handheld.stl]
